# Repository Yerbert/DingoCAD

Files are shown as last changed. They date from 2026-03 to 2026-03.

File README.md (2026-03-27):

<p align="center">
    
</p>

The Dingo is a low-cost robotic quadruped built using 35kg servo motors.

This was completed for a University Capstone Project by Nathan Ferguson and Alexander Calvert

Code and Bill Of Materials:
https://github.com/Yerbert/DingoQuadruped

Video:
https://youtu.be/8KntOIgzUjY

<p align="center">
    
</p>

Some build notes:
- The black piece which acts to transfer the motion of the lower servo to the lower leg should be printed in two parts, then have a bearing inserted, then be glued together. There are configurations in Solidworks to allow the export of this but I will try add all STLs soon.
- All parts in contact with the motors MUST be printed in ABS for temperature resistance. PLA parts will soften due to the heat the motors produce (although this may be avoided using the fans). So all orange parts are ABS as well as the black hub which holds the servos for the upper and lower leg. Note that the upper leg is in contact with the servos via the bolts which attach it so should also ideally be printed in ABS to avoid any issues.
- The rear upper and lower parts (large orange parts) that go aroudn the ports of the PI should be printed as a single piece. They were designed separate but you will get much better results just exporting the sub assembly as an STL and printing that
- All heat set inserts should be pushed in with a soldering iron tip. See here https://www.youtube.com/watch?v=hwq15qH-4x4
-
UPDATE: STEP file has now been added. STLs to come.

Special thanks to the open-source designs that helped inspire aspects of this project:
- Stanford Pupper V1: https://pupper.readthedocs.io/en/latest/index.html
- Stanford Pupper V2: https://pupper-independent-study.readthedocs.io/en/latest/
- Notspot: https://github.com/lnotspotl/notspot_sim_py
- Kangal: Diy quadruped robot
- SpotMicro: https://www.thingiverse.com/thing:3445283, https://spot-mini-mini.readthedocs.io/en/latest/index.html
- Nova SM3: https://novaspotmicro.com/
- Mini Pupper: https://minipupperdocs.readthedocs.io/en/latest/guide/Features.html

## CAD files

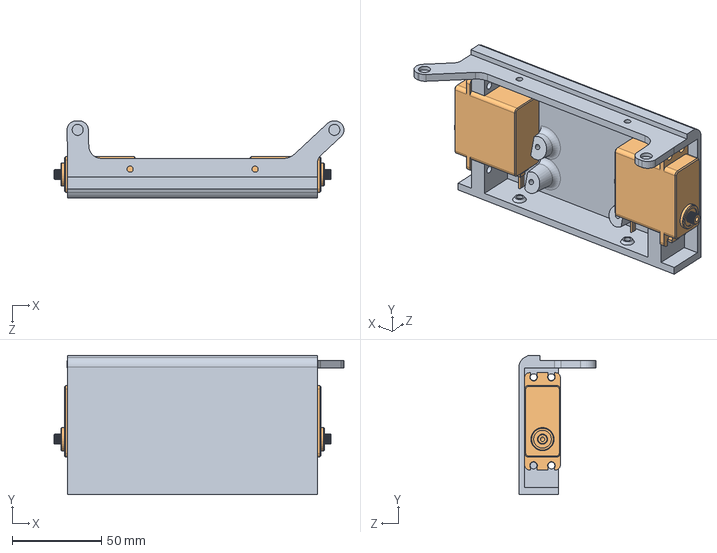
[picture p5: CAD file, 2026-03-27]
URDF File/URDF V3/Right Side Hip Servo Assembly.SLDASM
162.5 x 77.9 x 43.2 mm
Hip servo Hub For Right Hand Side
CLS6336 35kg servo x 2

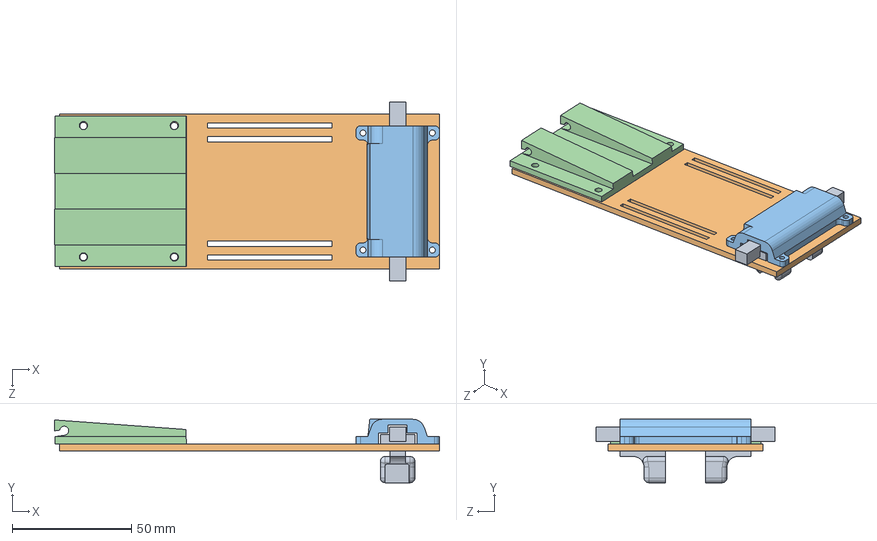
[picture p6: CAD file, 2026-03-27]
6. All other child Components/Battery Holder Flap/Battery Flap Assembly.SLDASM
161.1 x 26.6 x 74.8 mm
Battery Latch thumbpiece x 2
Battery Holder flap base ACRYLIC
Battery latch top cover
Battery flap rod support

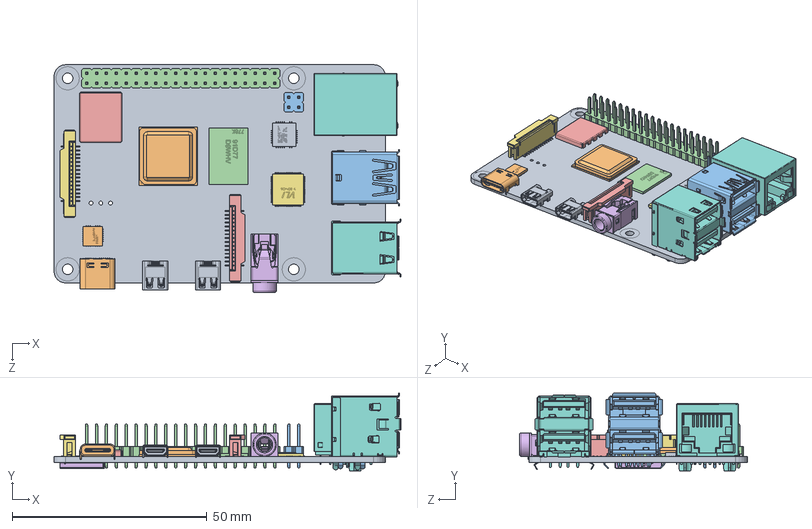
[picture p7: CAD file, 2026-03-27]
1. Off the shelf components/Raspberry Pi 4 Model B/Raspberry Pi 4 Model B.SLDASM
89.0 x 19.9 x 58.4 mm
PCB, RPi4ModelB
Broadcom BCM2711B0 CPU, RPi4ModelB
2.54 mm DUPONT MALE PIN HEADER, POE, 2X2, RPi4ModelB
2.54 mm DUPONT MALE PIN HEADER, IO, 2X20, RPi4ModelB
Camera Connector, RPi4ModelB
Microphone Plug, RPi4ModelB
Display Connector, RPi4ModelB
Gigabit Ethernet Port, RPi4ModelB
Female Micro HDMI Connector, RPi4ModelB x 2
Female USB Type C Connector, RPi4ModelB
2X USB3.0 PORTS, RPi4ModelB
91D77 D9WHV 778K, 4 GB LPDDR4 SDRAM, RPi4ModelB
Cypress CYW43455 Wireless Module Cover, RPi4ModelB
SD Card Slot, RPi4ModelB
VIA VL805 PCIe USB 3.0 controller, RPi4ModelB
2X USB2.0 PORTS, RPi4ModelB
Broadcom BCM54213PE Gigabit Ethernet Transceiver, RPi4ModelB
MxL7704 Universal PMIC, RPi4ModelB

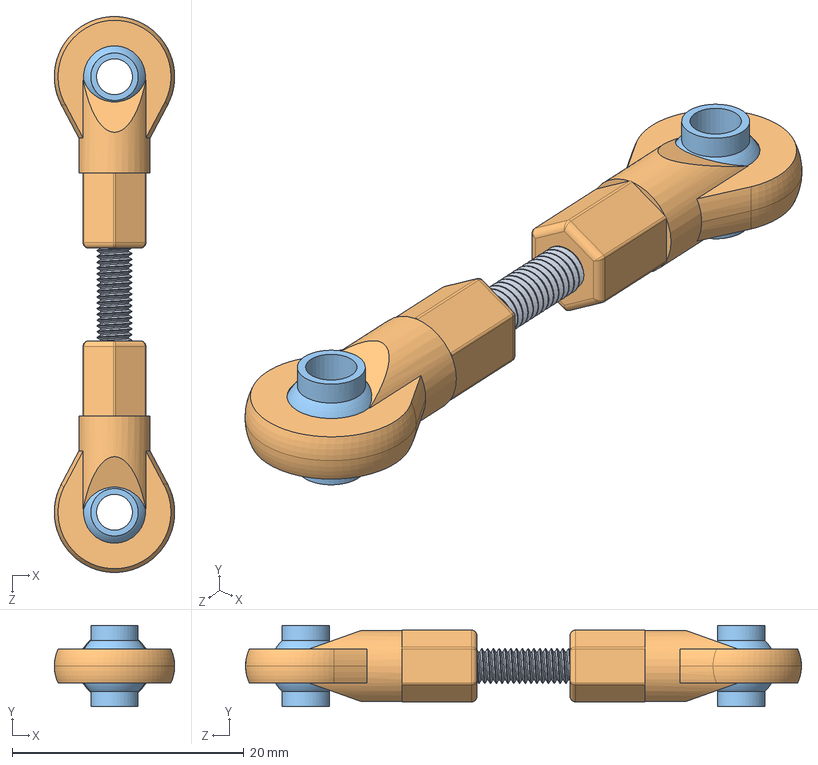
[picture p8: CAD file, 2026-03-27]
1. Off the shelf components/ball joint push rod/pull_joint_with_ball_42mm.SLDASM
10.4 x 7.00 x 48.0 mm
m3_threaded_rod_30mm
ball_head_joint_20mm x 2
ball_joint x 2

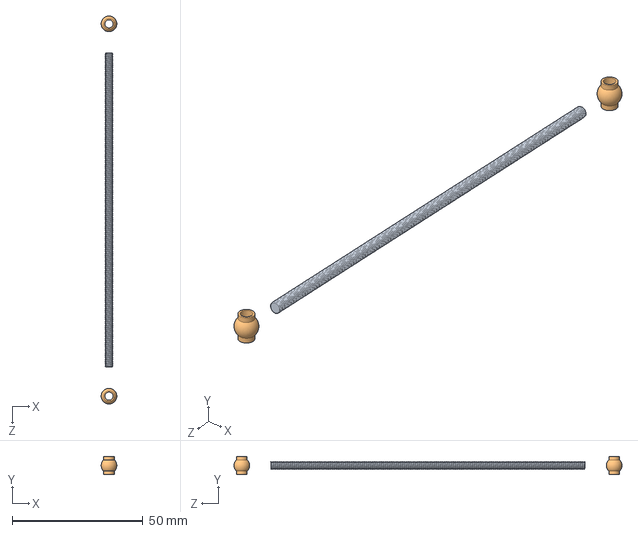
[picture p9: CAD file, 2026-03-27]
1. Off the shelf components/ball joint push rod/pull_joint_with_ball_142mm.SLDASM
6.00 x 7.00 x 148.2 mm
m3_threaded_rod_120mm
ball_joint x 2

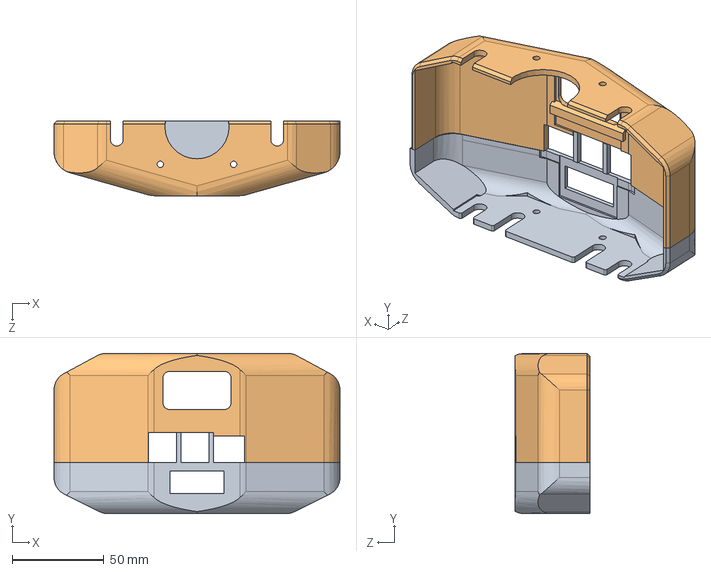
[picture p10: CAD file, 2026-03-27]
6. All other child Components/Back supports combined.SLDASM
156.0 x 87.5 x 40.6 mm
Torso - rear support
Torso - rear support upper

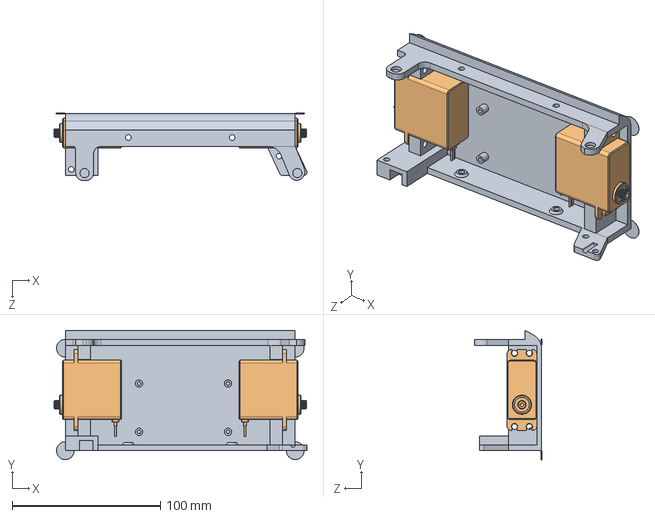
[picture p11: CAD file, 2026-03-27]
6. All other child Components/Left Side Hip Servo Assembly.SLDASM
170.6 x 87.1 x 45.2 mm
Hip servo Hub For Left Hand Side
CLS6336 35kg servo x 2

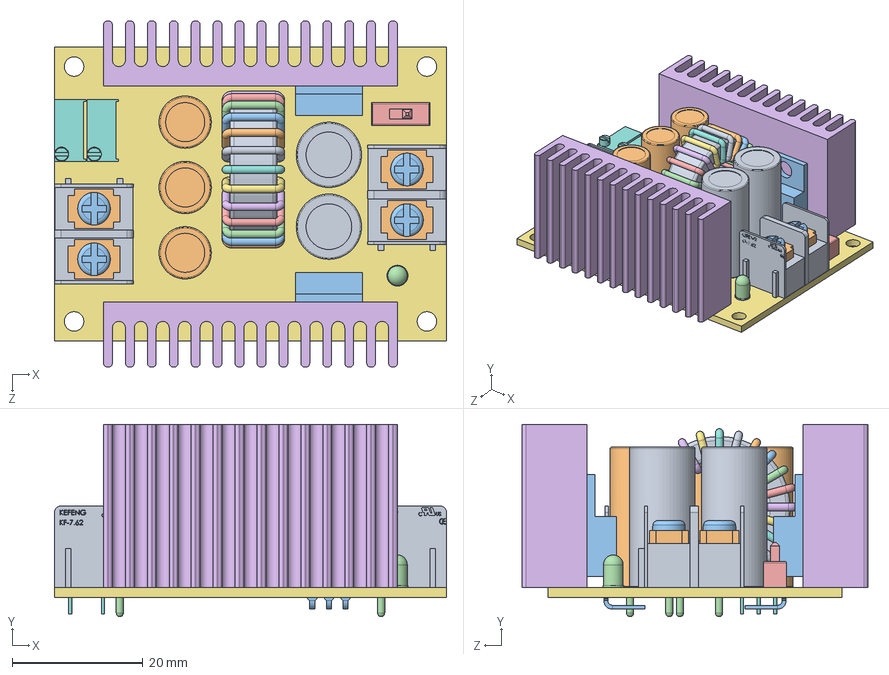
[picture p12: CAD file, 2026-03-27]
1. Off the shelf components/20 A Buck Converter/DC-DC Step Down Buck Converter CC-CV 300W 20A.step.SLDASM
60.0 x 29.5 x 53.0 mm
Base.step x 2
Arandela.step x 4
Tornillo.step x 4
Terminal.step x 4
Component35.step
Component16.step
Component17.step
Component18.step
Component19.step
Component20.step
Component21.step
Component22.step
Component23.step
Component24.step
Component25.step
Component26.step
Component27.step
Component28.step
Component29.step
Component30.step
Component31.step
Component32.step
Component33.step
Component34.step
Component11.step
Component12.step
Component13.step
Component14.step
Component15.step
heatsink.step x 2
pcb board.step
potentiometer.step x 2
elco-a.step x 2
elco-b.step x 3
transistor.step x 2
led.step
switch.step

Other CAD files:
1. Off the shelf components/ball joint push rod/Mirrorpull_joint_with_ball_142mm.SLDASM
2. Leg Components/MirrorRIGHT leg assembly.SLDASM
1. Off the shelf components/20 A Buck Converter/2-pin terminal_1.step.SLDASM
1. Off the shelf components/ball joint push rod/Mirrorpull_joint_with_ball_42mm1.SLDASM
1. Off the shelf components/20 A Buck Converter/2-pin terminal.step.SLDASM
1. Off the shelf components/ball joint push rod/Mirrorpull_joint_with_ball_42mm.SLDASM
1. Off the shelf components/20 A Buck Converter/inductor.step.SLDASM
1. Off the shelf components/ball joint push rod/Mirrorpull_joint_with_ball_142mm1.SLDASM
1. Off the shelf components/20 A Buck Converter/Component21.step.SLDPRT
1. Off the shelf components/ball joint push rod/MirrorIinvisible_servo_reference_mount.SLDPRT
1. Off the shelf components/20 A Buck Converter/Arandela.step.SLDPRT
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

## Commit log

2026-03-27 Added CAD files
    [AS 1420 - M2.5 x 12-N.SLDPRT, AS 1420 - M4 x 12-N.SLDPRT, AS 1420 - M4 x 25-N.SLDPRT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]
2026-03-27 Adding remaining files
    [2-pin terminal.step.SLDASM, 2-pin terminal_1.step.SLDASM, 2.54 mm DUPONT MALE PIN HEADER, IO, 2X20, RPi4ModelB.SLDPRT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]
